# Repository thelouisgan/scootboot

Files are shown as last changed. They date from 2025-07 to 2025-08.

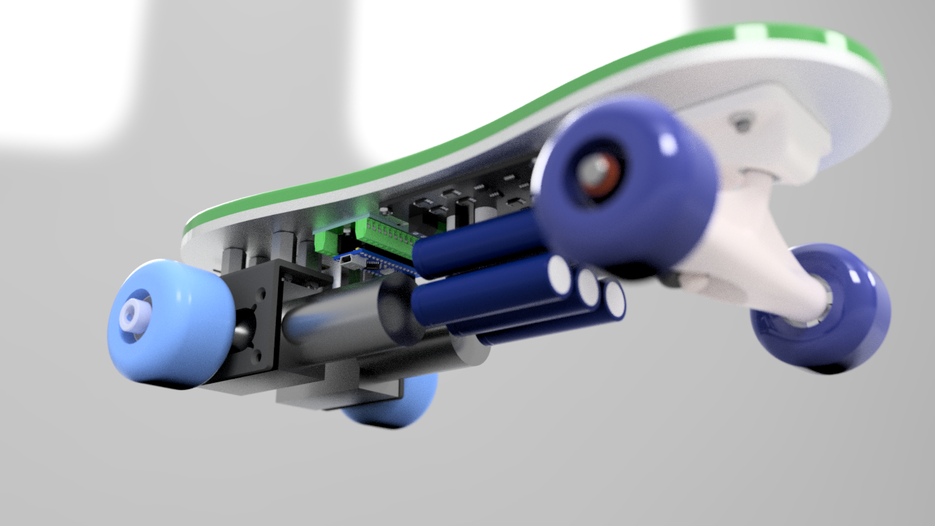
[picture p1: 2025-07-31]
designs-and-renders/scootboot v11 render-elec.png

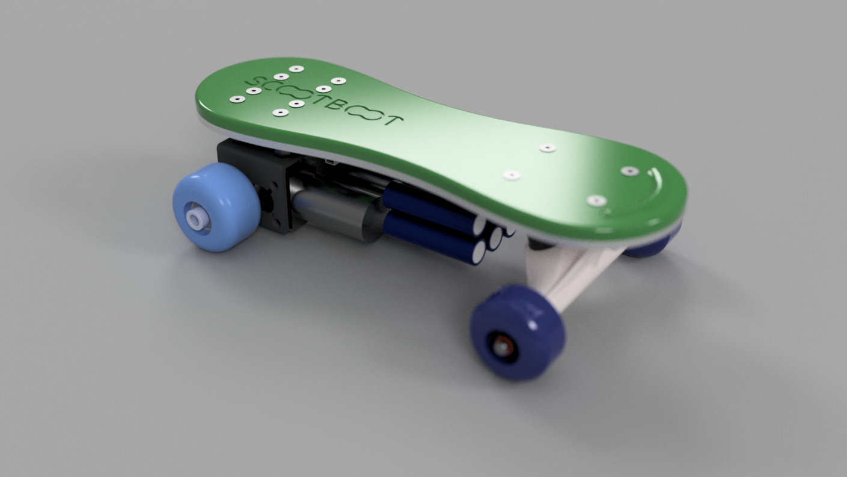
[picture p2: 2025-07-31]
designs-and-renders/scootboot v11 render_homeview.png

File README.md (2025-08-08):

Asset 2@4x-8

---
Powered attachment to shoes using motorised wheels to accelerate walking speeds

Driven by 2 rear DC motors with over 64kg.cm of torque, this attaches to your shoes with simple velcro but provides an increased assistance to your pace. This project was inspired by Shift Robotics' Moonwalkers but controlled though an RC and powered by an Arduino Nano. These boots are able to make walking much faster and acts as a travellator but on any terrain.

Screenshot 2025-08-01 at 1 14 32 AM
Screenshot 2025-07-31 at 11 46 31 PM
Screenshot 2025-07-31 at 11 48 00 PM

# Electronics schematic
scootboot_schem

# BOM
| Part Name | Unit Cost (MYR) | Qty | Total Cost (MYR) | Total Cost (USD) | Product Link |
|---|---|-----|---|---|---|
| 5840-31ZY 51MM Brushed DC Worm Gear Reduction Motor - 12V 60RPM Single Motor | RM82.64 | 4 | RM330.56 | $78.05 | [Shopee](https://shopee.com.my/product/1079294791/25333786998/) |
| 5840 Motor mount bracket INCLUDED | RM0.00 | 4 | RM0.00 | $0.00 | [Shopee](https://shopee.com.my/product/1079294791/25333786998/) |
| MDD10A 10A 5V-30V DC Motor Driver (Dual Channel) | RM94.00 | 2 | RM188.00 | $44.39 | [Cytron](https://my.cytron.io/p-10amp-5v-30v-dc-motor-driver-2-channels) |
| 5.25in Aluminium Skateboard Truck | RM20.98 | 2 | RM41.96 | $9.91 | [Shopee](https://shopee.com.my/Black-Skateboard-Truck-Long-Plate-Bridge-Base-Surfboard-steering-bracket-Hardware-i.1425994592.27470595967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) |
| KISSONE SKATEBOARD WHEEL A CUT PRO 101A 53MM 52MM 4PCS | RM48.09 | 1 | RM48.09 | $11.36 | [Shopee](https://shopee.com.my/KISSONE-SKATEBOARD-WHEEL-A-CUT-PRO-101A-53MM-52MM-4PCS-i.233633652.29601886745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) |
| 35x2cm Fastening Velcro Cable Straps - 10 pack | RM7.77 | 1 | RM7.77 | $1.83 | [Shopee](https://shopee.com.my/Reusable-Fastening-Cable-Straps-and-Organize-Cords-Cable-Ties-Set-10-30-Pack-Adjustable-Multi-Purpose-Hook-and-Loop-Cord-Ties-to-Keep-Cords-Org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) |
| ATmega328P Arduino Nano compatible V3.0 | RM18.00 | 2 | RM36.00 | $8.50 | [Shopee](https://shopee.com.my/Nano-V3.0-ATmega328P-controller-compatible-for-arduino-nano-CH340-USB-driver-with-Cable-i.42740247.42701321834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) |
| 3S2P 12V 12800mAh 18650 Li-ion Rechargable battery with BMS | RM45.00 | 2 | RM90.00 | $21.25 | [Shopee](https://shopee.com.my/Jungla-3S2P-12V-12800mAh-battery-18650-Li-ion-12.8-Ah-Rechargeable-batteries-with-BMS-Lithium-JNOZ-L-i.1518479837.43251239041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) |
| ELRS MINI 915Mhz Receiver NANO ExpressLRS RX T type Antenna - 2 PACK | RM96.79 | 1 | RM96.79 | $22.85 | [Shopee](https://shopee.com.my/ELRS-MINI-915Mhz-Receiver-NANO-ExpressLRS-RX-T-type-Antenna-For-RC-FPV-Long-Range-Racing-Drone-Quadcopter-i.911670347.29822254765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) |
| Nano I/O Expansion Shield with Terminal Adapter Block Screw | RM5.90 | 2 | RM11.80 | $2.79 | [Shopee](https://shopee.com.my/-NEW-SOLDERED-Nano-I-O-Pin-Expansion-Terminal-Adapter-Block-Screw-Shield-V1.0-for-Arduino-i.33091591.463168396) |
| TPU Sole 3D Printing incl. shipping | RM101.24 | 2 | RM202.48 | $47.81 | [3D Express](https://3dexpress.my/services/) |
| CNC Aluminium baseplate | RM100.00 | 2 | RM200.00 | $47.23 | [Shopee](https://shopee.com.my/product/865167118/20251343704) |

**Total Cost (MYR): RM1,253.45**  
**Total Cost (USD): $295.97**

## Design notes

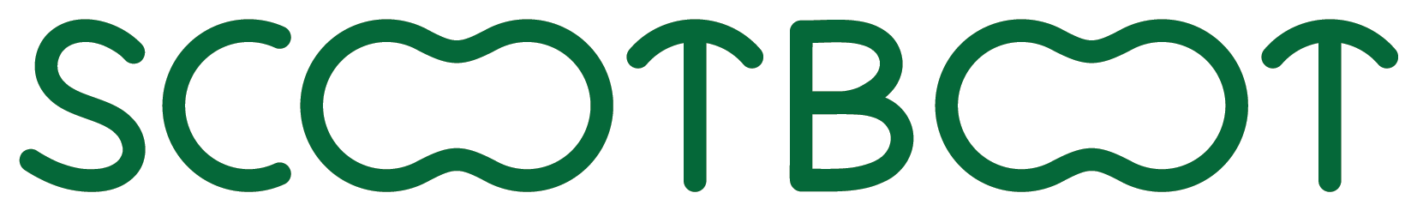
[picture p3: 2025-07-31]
designs-and-renders/Asset 2@4x-8.png

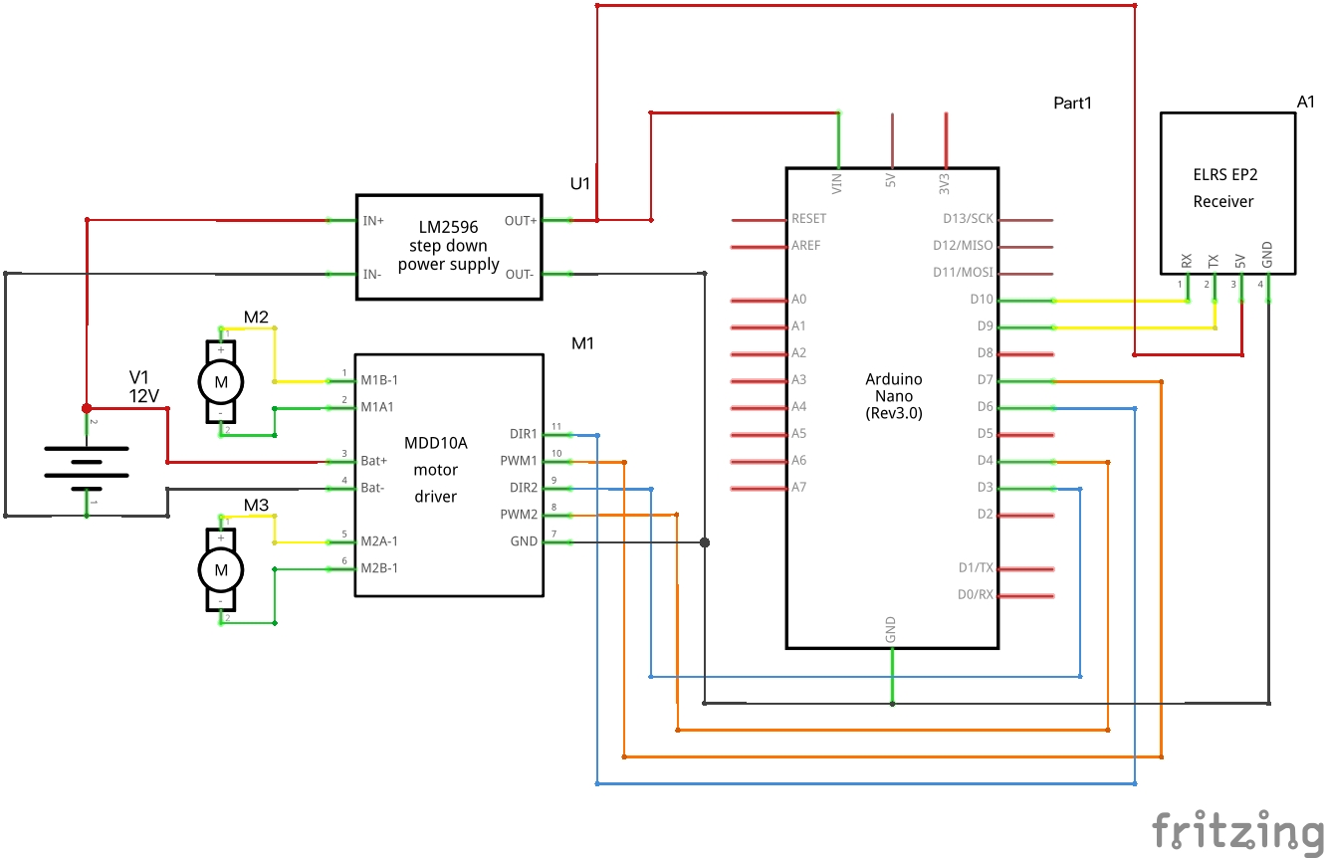
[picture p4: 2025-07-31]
firmware-and-electronics/scootboot_schem.jpg

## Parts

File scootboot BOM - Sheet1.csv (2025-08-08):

Part Name - NOT INCLUDING SHIPPING/TAX | Unit Cost (Malaysian Ringgit) | Quantity | Total Cost | Total Cost (USD) | Product Link
5840-31ZY 51MM Brushed DC Worm Gear Reduction Motor - 12V 60RPM Single Motor | RM82.64 | 4 | RM330.56 | $78.05 | https://shopee.com.my/product/1079294791/25333786998/
5840 Motor mount bracket INCLUDED | RM0.00 | 4 | RM0.00 | $0.00 | https://shopee.com.my/product/1079294791/25333786998/
MDD10A 10A 5V-30V DC Motor Driver (Dual Channel) | RM94.00 | 2 | RM188.00 | $44.39 | https://my.cytron.io/p-10amp-5v-30v-dc-motor-driver-2-channels
5.25in Aluminium Skateboard Truck | RM20.98 | 2 | RM41.96 | $9.91 | https://shopee.com.my/Black-Skateboard-Truck-Long-Plate-Bridge-Base-Surfboard-steering-bracket-Hardware-i.1425994592.27470595967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
KISSONE SKATEBOARD WHEEL A CUT PRO 101A 53MM 52MM 4PCS | RM48.09 | 1 | RM48.09 | $11.36 | https://shopee.com.my/KISSONE-SKATEBOARD-WHEEL-A-CUT-PRO-101A-53MM-52MM-4PCS-i.233633652.29601886745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
35x2cm Fastening Velcro Cable Straps - 10 pack | RM7.77 | 1 | RM7.77 | $1.83 | https://shopee.com.my/Reusable-Fastening-Cable-Straps-and-Organize-Cords-Cable-Ties-Set-10-30-Pack-Adjustable-Multi-Purpose-Hook-and-Loop-Cord-Ties-to-Keep-Co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
ATmega328P Arduino Nano compatible V3.0 | RM18.00 | 2 | RM36.00 | $8.50 | https://shopee.com.my/Nano-V3.0-ATmega328P-controller-compatible-for-arduino-nano-CH340-USB-driver-with-Cable-i.42740247.42701321834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
3S2P 12V 12800mAh 18650 Li-ion Rechargable battery with BMS | RM45.00 | 2 | RM90.00 | $21.25 | https://shopee.com.my/Jungla-3S2P-12V-12800mAh-battery-18650-Li-ion-12.8-Ah-Rechargeable-batteries-with-BMS-Lithium-JNOZ-L-i.1518479837.43251239041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
ELRS MINI 915Mhz Receiver NANO ExpressLRS RX T type Antenna - 2 PACK | RM96.79 | 1 | RM96.79 | $22.85 | https://shopee.com.my/ELRS-MINI-915Mhz-Receiver-NANO-ExpressLRS-RX-T-type-Antenna-For-RC-FPV-Long-Range-Racing-Drone-Quadcopter-i.911670347.29822254765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
Nano I/O Expansion Shield with Terminal Adapter Block Screw | RM5.90 | 2 | RM11.80 | $2.79 | https://shopee.com.my/-NEW-SOLDERED-Nano-I-O-Pin-Expansion-Terminal-Adapter-Block-Screw-Shield-V1.0-for-Arduino-i.33091591.463168396
TPU Sole 3D Printing incl. shipping | RM101.24 | 2 | RM202.48 | $47.81 | https://3dexpress.my/services/
CNC Aluminium baseplate | RM100.00 | 2 | RM200.00 | $47.23 | https://shopee.com.my/product/865167118/20251343704
 |  |  | RM1,253.45 | $295.97

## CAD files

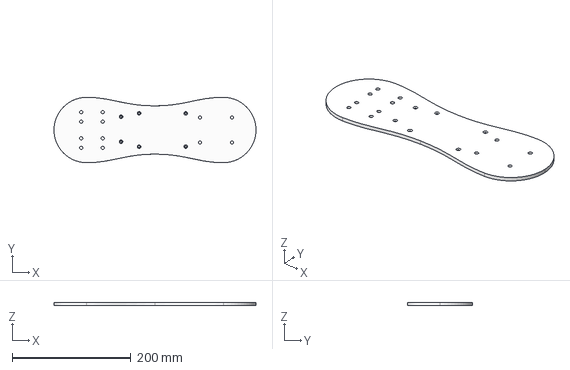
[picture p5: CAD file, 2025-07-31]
models/Baseplate CNC scootboot v11.step
340.0 x 110.0 x 5.00 mm

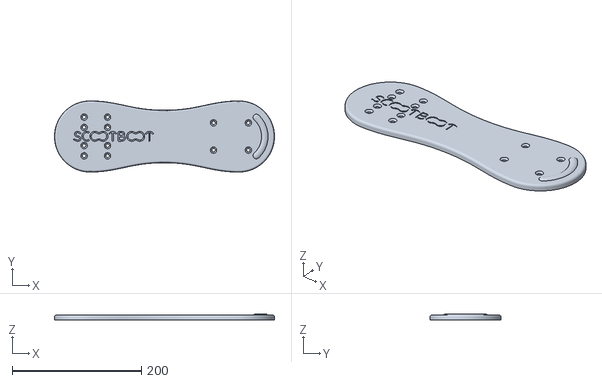
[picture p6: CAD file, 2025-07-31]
models/TPU Sole scootboot v11.stl
340.0 x 110.0 x 10.0

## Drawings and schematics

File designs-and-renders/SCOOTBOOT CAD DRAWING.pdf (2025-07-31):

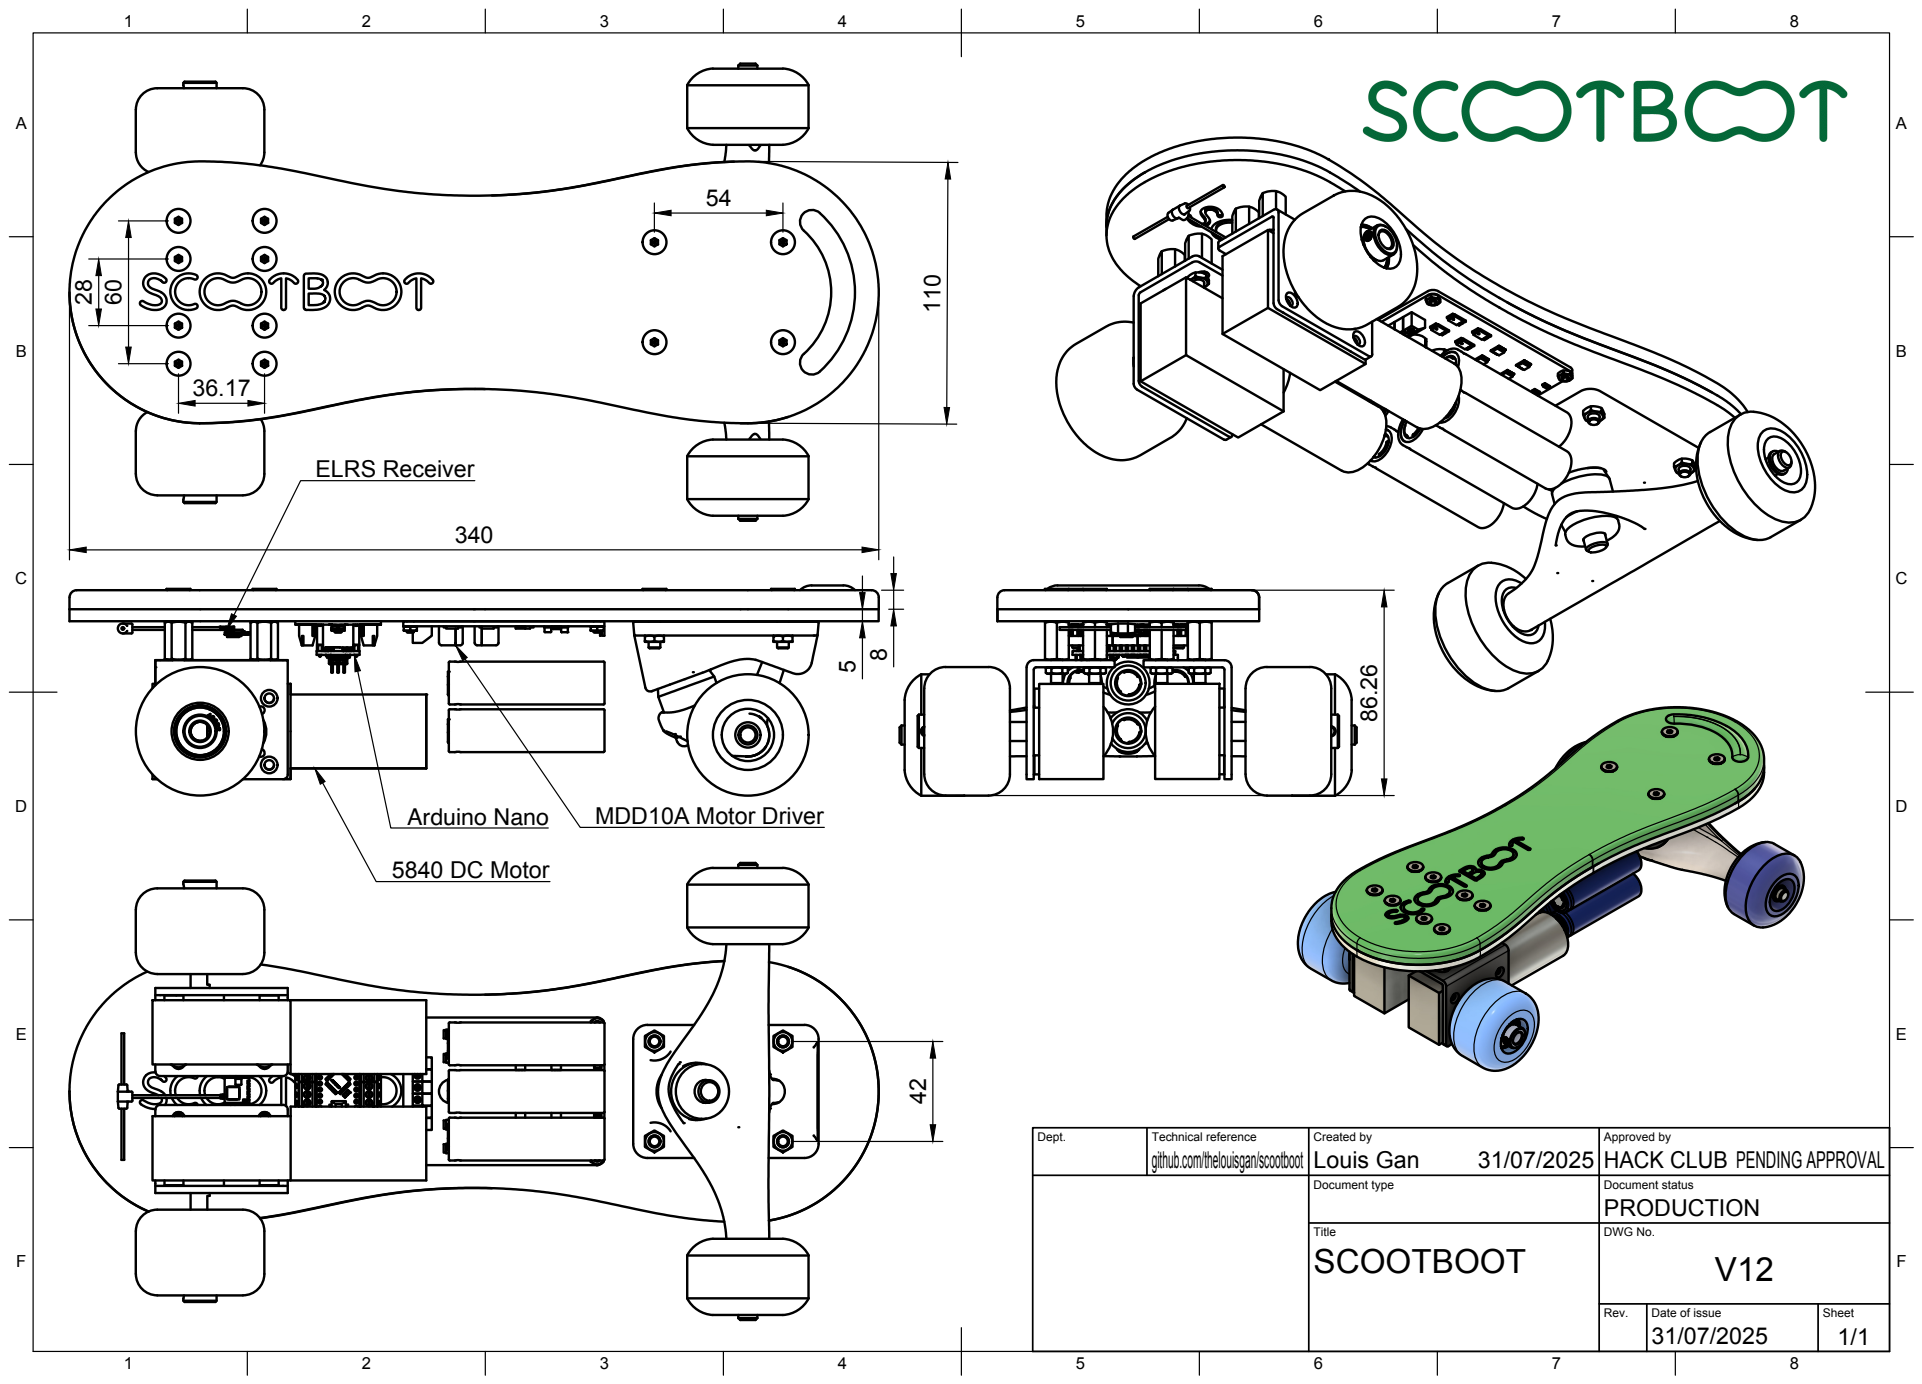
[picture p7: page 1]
Dept.; Technical reference; Created by; Approved by; Document type; Document status; Title; DWG No.; Rev.; Date of issue; Sheet; PENDING APPROVAL; github.com/thelouisgan/scootboot Louis Gan; HACK CLUB; Arduino Nano; MDD10A Motor Driver; 5840 DC Motor; ELRS Receiver

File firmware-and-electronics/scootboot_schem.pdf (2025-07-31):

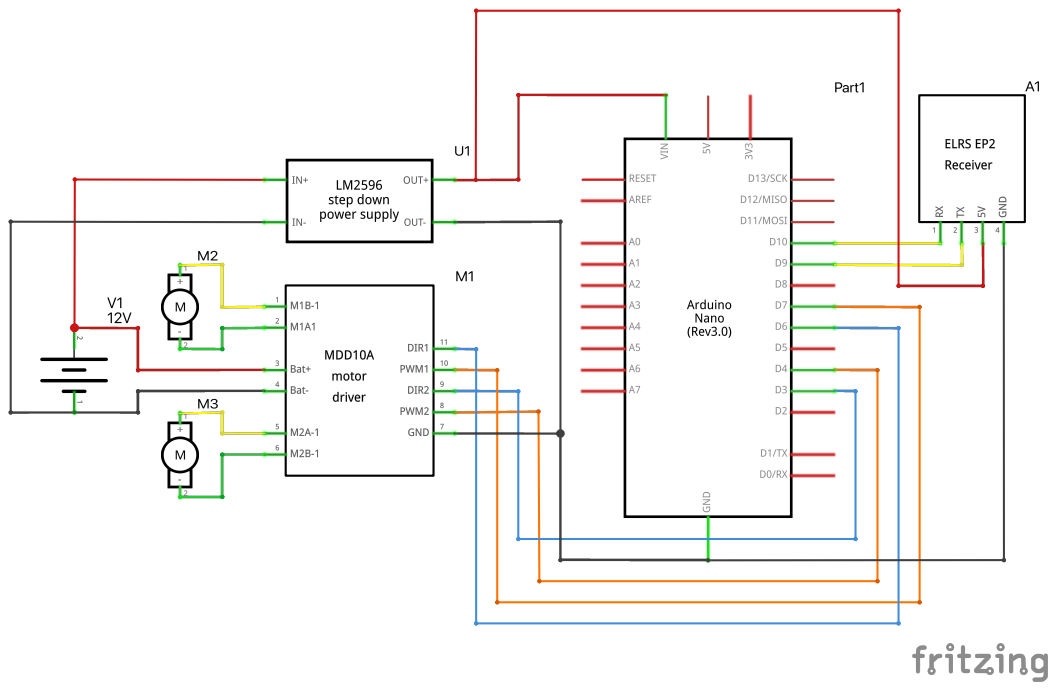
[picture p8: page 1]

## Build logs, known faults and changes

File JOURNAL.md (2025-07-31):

---
title: "Scootboot"
author: "@louisgan"
description: "Powered attachment to shoes using motorised wheels to accelerate walking speeds"
created_at: "2025-07-14"
---

# 21 hours total (design+research)

## 18/07/2025 - 2 hours
### Researching, creating plan and initial BOM list

- I want to create my own DIY moonwalker boots, basically motor powered wheels attached to bottom of shoes
- Use metal baseplate and attach to shoes with velcro, with motor + electronics and battery on the baseplate
- Speed is controlled manually via RF using EdgeTX controller + RX which I have, so different from AI-powered smart speed control from [Moonwalkers](https://shiftrobotics.io/products/moonwalkers?srsltid=AfmBOoqtUeJfdKixhwpnNn_zGu1JXuPLj22AJFjQfRdvFxCT6fvGAdw2)
- Preferably Arduino or Raspberry Pi powered
- Motor mounted on the side, preferably have 4 wheels per boot and the back two wheels are motorised
- I want to use drone/RC car style LiPo battery 12V
- Factor in motor type, size, power, compatibility, feasibleness, and wheels
- If motor on side, will it be able to support wearer's weight up to eg. 60–80kg? or will the motor shaft attached to wheel be not strong enough and collapse
- Will torque be enough / speed?
- I could use rubber or skateboard wheels (Polyurethane)
- I want it to lightly assist in my walking like a travellator – so increase by a few km/h to my walking speed

**BOM per wheel:**
| Component | Specs / Notes | Qty | Unit Price (USD) | Total (USD) |
| --- | --- | ----- | --- | --- |
| **DC Gear Motor** | 12V, 100 RPM, 10 Nm torque, 8mm shaft | 2 | \$18 | \$36 |
| **Motor Mount Bracket** | L-bracket steel, supports 775/550 motors | 2 | \$3 | \$6 |
| **Motor Shaft Coupler** | 8mm bore to wheel hub | 2 | \$4 | \$8 |
| **Wheels (longboard-style)** | 70mm–90mm polyurethane skateboard wheels with 608zz bearings | 4 | \$6 | \$24 |
| **Baseplate (Metal)** | Aluminum, 3mm thick (cut to size \~30x10 cm) | 1 | \$10 | \$10 |
| **Velcro Straps + Padding** | Heavy-duty | 2 | \$5 | \$10 |
| **Arduino Nano** | With CH340, for compactness | 1 | \$3 | \$3 |
| **Dual Channel Motor Driver** | 12V 10A BTS7960 or Cytron MD10C | 1 | \$10 | \$10 |
| **LiPo Battery** | 3S 12.6V 2200–3000mAh 30C | 1 | \$20 | \$20 |
| **Voltage Regulator** | 5V buck converter (for Arduino) | 1 | \$2 | \$2 |
| **XT60 Connectors + Wires** | Power wiring | 1 set | \$2 | \$2 |
| **Power Switch** | Toggle with XT60 inline | 1 | \$2 | \$2 |
| **Receiver (EdgeTX compatible)** | Already owned | 0 | \$0 | \$0 |

Not including shipping/tax
Estimated total cost per boot: $133 USD
Estimated total cost for 1 pair: $266 USD

## 19/07/2025 - 2 hours
### Motor research & parts sourcing

[5840-31ZY Worm Gear Motor](https://shopee.com.my/5840-31ZY-Worm-Gear-Motor-12V-24V-Bidirectional-Short-Shaft-Forward-And-Reverse-7RPM~470RPM-Speed-Regulating-Metal-Gear-Motor-Micro-DC-Brushed-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)
12V 60RPM including Motor Bracket
| Reduction ratio | Rated voltage  | Speed (RPM ±10%)  | Current (A) | Torque (KGfCM) | Power (W) |
| --- | ---  | ---  | --- | --- | --- |
| 100 | 12 | 60 | 1.6 | 16 | 19.2 |

Screenshot 2025-07-21 at 5 09 03 PM
Screenshot 2025-07-21 at 5 09 25 PM


MYR 72.39 = 17.09 USD
x4 = MYR 289.56 = 68.36 USD

-----------------------

12V/24V Large Torque 0.5KG.CM~100KG.CM 32GP-31ZY Micro Reduction DC Planetary Brush Motor
| Reduction ratio | Rated voltage  | Speed (RPM ±10%)  | Current (A) | Torque (KGfCM) | Power (W) |
| --- | ---  | ---  | --- | --- | --- |
| 100 | 12 | 65 | 1.8 | 14 | 21.6 |
8mm shaft diameter

Screenshot 2025-07-21 at 5 30 18 PM
Screenshot 2025-07-21 at 5 30 47 PM

Mass 335g, gearbox length 38mm
Larger footprint with added joints
Requires universal joint for 90deg shaft coupling

-----------------------

### Motor driver
**Cytron 13A Dual Channel Motor Driver - MDD10A**



MYR 94.00 = USD 22.21
X2 = MYR 188 = USD 44.42

## 25/07/2025 - 2 hours
### Sketching exploded diagram & plan

Screenshot 2025-07-25 at 8 25 25 PM

## 27/07/2025 - 2 hours
### Designing base plate shape and logo

Screenshot 2025-07-28 at 2 26 02 AM

## 28/07/2025 - 3.5 hours
### CAD Modelling of rear wheels and component research

Screenshot 2025-07-29 at 9 38 43 PM

For the shaft coupling between the polyurethane wheels and the motor axle, I decided to weld the built in bearing to so that the torque is able to be transferred while allowing me to weld the 8mm motor axle directly into the 8mm bore for the inner bearing track. To prevent lateral slipping, I will be purchasing and using set screw collars outside the wheels on the axle, which I will purchase the longer 51mm shaft length for easier mounting.

## 29/07/2025 - 2 hours
### CAD for all electronics, front wheels and aluminium baseplate

Screenshot 2025-07-30 at 1 15 26 AM
Screenshot 2025-07-30 at 1 15 39 AM

## 30/07/2025 - 4.5 hours (correction from wakatime)
### Finished design for Aluminium baseplate (CNC) and TPU sole (3D print) milling + mounting holes

**Rear wheels mounting bracket:**
 - 8x M5x40 Countersunk Head Cap Screw
 - [8x Female Threaded Hex Standoff, 18-8 Stainless Steel, 10mm Hex, 16mm Long, M5 x 0.8mm Thread](https://www.mcmaster.com/94868A632/)
 - 8x M5X0.8 Chamfered Hexagon Thin Nut

**Front truck mounting bolts**
 - 4x M5x40 Countersunk Head Cap Screw
 - 4x M5X0.8 Chamfered Hexagon Thin Nut

**Electronics PCB (Arduino Nano + MDD10A Motor Driver)**
 - 6x M3X10 Countersunk Head Cap Screw
 - 6x M3X0.5 Chamfered Hexagon Thin Nut

Screenshot 2025-07-31 at 1 35 54 AM
Screenshot 2025-07-31 at 1 35 05 AM
Screenshot 2025-07-30 at 7 45 59 PM
Screenshot 2025-07-31 at 1 52 35 AM

## 31/07/2025 - 3 hours
### Designing electronics schematic and firmware

scootboot_schem

- Ready to purchase parts and build

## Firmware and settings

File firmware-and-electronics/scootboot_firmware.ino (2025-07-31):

#include <SoftwareSerial.h>

const int MOTOR_PWM1_PIN = 7;
const int MOTOR_DIR1_PIN = 6;
const int MOTOR_PWM2_PIN = 4;
const int MOTOR_DIR2_PIN = 3;

// ELRS rx
SoftwareSerial elrsSerial(10, 9); // RX-D10   TX-D9

int throttleValue = 0;
int auxValue = 0;
bool motorsEnabled = false;

unsigned long lastRXUpdate = 0;
const unsigned long RX_TIMEOUT = 1000;

const int MIN_MOTOR_SPEED = 0;
const int MAX_MOTOR_SPEED = 180;  // max->255
const int DEADBAND = 50;

// CRSF protocol values
uint16_t channelData[16];

void setup() {
  Serial.begin(115200);
  elrsSerial.begin(420000);

  pinMode(MOTOR_PWM1_PIN, OUTPUT);
  pinMode(MOTOR_DIR1_PIN, OUTPUT);
  pinMode(MOTOR_PWM2_PIN, OUTPUT);
  pinMode(MOTOR_DIR2_PIN, OUTPUT);

  stopMotors();
  
  Serial.println("SCOOTBOOT active");
  Serial.println("Waiting for RC signal...");
}

void loop() {
  readCRSF();
  
  // Signal loss check
  if (millis() - lastRXUpdate > RX_TIMEOUT) {
    motorsEnabled = false;
    stopMotors();
    Serial.println("SIGNAL LOST, MOTORS DISABLED");
    delay(100);
    return;
  }
  
  if (motorsEnabled) {
    controlMotors();
  } else {
    stopMotors();
  }

  //debug
  if (millis() % 200 == 0) {
    Serial.print("Throttle: ");
    Serial.print(throttleValue);
    Serial.print(" | Aux: ");
    Serial.print(auxValue);
    Serial.print(" | Enabled: ");
    Serial.println(motorsEnabled ? "YES" : "NO");
  }
  
  delay(20);
}

void readCRSF() {
  static uint8_t buffer[64];
  static uint8_t bufferIndex = 0;
  
  while (elrsSerial.available()) {
    uint8_t byte = elrsSerial.read();
    
    if (bufferIndex == 0 && byte != 0xC8) {
      continue;
    }
    
    buffer[bufferIndex++] = byte;
    
    if (bufferIndex >= 2 && bufferIndex >= buffer[1] + 2) {
      if (buffer[2] == 0x16) { // RC channels frame
        parseCRSFChannels(&buffer[3], buffer[1] - 2);
        lastRXUpdate = millis();
      }
      bufferIndex = 0;
    }
    
    if (bufferIndex >= 64) {
      bufferIndex = 0;
    }
  }
}

void parseCRSFChannels(uint8_t* payload, uint8_t length) {
  if (length >= 22) {
    channelData[0] = ((payload[0] | payload[1] << 8) & 0x07FF);
    channelData[1] = ((payload[1] >> 3 | payload[2] << 5) & 0x07FF);
    channelData[2] = ((payload[2] >> 6 | payload[3] << 2 | payload[4] << 10) & 0x07FF);
    channelData[3] = ((payload[4] >> 1 | payload[5] << 7) & 0x07FF);
    
    throttleValue = map(channelData[0], 172, 1811, -255, 255);
    auxValue = map(channelData[1], 172, 1811, 1000, 2000);
    
    motorsEnabled = (auxValue > 1500);
  }
}

void controlMotors() {
  int motorSpeed = 0;
  bool forward = true;
  
  if (abs(throttleValue) < DEADBAND) {
    motorSpeed = 0;
  } else {
    if (throttleValue > 0) {
      forward = true;
      motorSpeed = map(throttleValue, DEADBAND, 255, MIN_MOTOR_SPEED, MAX_MOTOR_SPEED);
    } else {
      forward = false;
      motorSpeed = map(abs(throttleValue), DEADBAND, 255, MIN_MOTOR_SPEED, MAX_MOTOR_SPEED/2);
    }
  }
  
  digitalWrite(MOTOR_DIR1_PIN, forward ? HIGH : LOW);
  digitalWrite(MOTOR_DIR2_PIN, forward ? HIGH : LOW);
  
  analogWrite(MOTOR_PWM1_PIN, motorSpeed);
  analogWrite(MOTOR_PWM2_PIN, motorSpeed);
}

void stopMotors() {
  analogWrite(MOTOR_PWM1_PIN, 0);
  analogWrite(MOTOR_PWM2_PIN, 0);
  digitalWrite(MOTOR_DIR1_PIN, LOW);
  digitalWrite(MOTOR_DIR2_PIN, LOW);
}

void emergencyStop() {
  motorsEnabled = false;
  stopMotors();
  Serial.println("EMERGENCY STOP ACTIVATED");
  
  for (int i = 0; i < 10; i++) {
    digitalWrite(LED_BUILTIN, HIGH);
    delay(100);
    digitalWrite(LED_BUILTIN, LOW);
    delay(100);
  }
}

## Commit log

2025-07-31 3D CAD Model
2025-07-31 Rename scootboot v11.step to 3D CAD MODEL scootboot v11.step
    [3D CAD MODEL scootboot v11.step]
2025-08-03 Folder reorganizing
    [Baseplate CNC scootboot v11.step, TPU Sole scootboot v11.stl, scootboot.fzz]
